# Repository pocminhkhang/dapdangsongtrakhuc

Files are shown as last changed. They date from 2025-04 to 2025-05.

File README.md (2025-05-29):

# ĐẬP DÂNG SÔNG TRÀ KHÚC
Dự án vận hành mô hình đập dâng sông Trà Khúc - Quảng Ngãi

Lĩnh vực dự thi:
-	Phần mềm tin học.
-	Các giải pháp kỹ thuật nhằm ứng phó với biến đổi khí hậu, bảo vệ môi trường và phát triển kinh tế

Giáo viên hướng dẫn:
    Lê Thị Như Huyền 
    SĐT: 0935745789
Tác giả:				Lớp:
    Trần Hoàng Minh Khánh	7B4
    Trần Hoàng Minh Khang	7B4
    Hoàng Minh Tuấn		7B4

IMG_20250529_091230~2

IMAGE ALT TEXT HERE (https://www.youtube.com/watch?v=1BTI75vWhXs)

A.	Ý TƯỞNG:
Nhiều lần cả nhà đi biển, ba em giới thiệu đập dâng và giải thích công dụng của nó. Anh em chúng em rất hứng thú, mong muốn được thấy nước sông dâng lên sẽ rất đẹp. Chờ đợi cũng lâu nhưng chưa thấy đập dâng hoạt động, thành phố Quảng Ngãi vào mùa nắng trơ trọi lòng sông, vậy là 3 anh em chúng em rủ nhau thực hiện dự án vận hành nó (đập dâng sông Trà Khúc)
Ban đầu chúng em chỉ nghĩ đến việc vận hành ngăn nước, xả nước sao cho nước dâng lên – hạ xuống như mong muốn là được. Tuy nhiên trong quá trình tìm hiểu thì mọi chuyện không đơn giản như vậy, trong các video em tìm hiểu được trên mạng về các con đập lớn, người ta đã phải làm cầu cá nhằm đảm bảo tính tự nhiên của hệ sinh thái dòng sông, do vậy đập dâng mô hình phải có cầu cá cho cá bơi ngược dòng về thượng nguồn, đập dâng phải vận hành hoàn toàn tự động theo mực nước thượng nguồn, điều tiết dòng chảy xuống hạ lưu làm sao để không bị nước biển xâm nhập, …
B.	CẤU TẠO MÔ HÌNH SẢN PHẨM
I.	Nguyên vật liệu làm mô hình:

	Tên vật tư	ĐVT	SL	Đơn giá	Thành tiền	Ghi chú
1	Tấm nền (40x80)	Cái	1	100,000 	100,000 	 
2	Sốp dùng làm bờ sông, núi	Tấm	5	20,000 	100,000 	 
3	Làm các phần của đập dâng	Bộ	5	20,000 	100,000 	 
4	Cảm biến mưa	Bộ	1	26,000 	26,000 	 
5	Cảm biến JDS	Bộ	1	81,000 	81,000 	 
6	Cảm biến khoảng cách	Bộ	3	32,000 	96,000 	 
7	Công tắt	Cái	1	2,000 	2,000 	 
8	Servo MG90S	Cái	4	35,000 	140,000 	 
9	Màn hình HMI 2.8inch cảm ứng tích hợp chip ESP32	Cái	1	260,000 	260,000 	 
10	Mạch mở rộng I2C	Cái	1	12,000 	12,000 	 
11	Cầu cá	Cái	1	30,000 	30,000 	 
12	Chip lập trình nhúng ESP32	Cái	1	  88,000 	88,000 	
13	Pin 18650	Cái	1	36,000 	36,000 	 
14	Mạch sạc pin 18650	Cái	1	16,000 	16,000 	 
-	Tổng tiền chi phí nguyên vật liệu: 1.087.000 đ
II.	 Cách lắp ráp, lắp đặt sản phẩm
1.	Mô hình núi, dòng sông, biển:
-	Núi: Làm từ sốp, đắp nhiều lớp lên rồi dùng dao gọt, tạo hình ngọn núi.
-	Bờ sông: Dùng sốp đắp dọc theo 2 bờ tấm nền để tạo bờ sông, hình thành lòng sông và biển ở cuối dòng.
-	Thời gian hoàn thành: 5 ngày
2.	Đảo Ngọc:
-	Dùng sốp làm hòn đảo giữ dòng sông, mô phỏng theo hình Đảo Ngọc thực tế.
-	Thời gian hoàn thành: 1 ngày
3.	Mô hình đập dâng:
-	Đập dâng được làm từ sốp dựng 4 trụ cao, lắp 2 tấm nhựa làm mô hình tấm chắn nước được cắm vào trụ đập.
-	Gắn 3 servo Mg290s vào các trụ như mô hình, 2 servo móc vào 2 tấm nhựa chắn nước, servo còn lại gắn vào mô hình cầu cá
-	Thời gian hoàn thành: 5 ngày
4.	Mô hình cầu cá: 
-	Mô hình cầu cá được làm từ sốp, tạo các bậc thang từ trên xuống dưới, khoét tạo hộc chứa nước, tạo hướng nước chảy 2 bên
-	Thời gian hoàn thành: 3 ngày
5.	Thiết bị đo mực nước:
-	Thiết bị đo mực nước sử dụng cảm biến đo khoảng cách, được cắm vào chip lập trình nhúng ESP32 Dev module và lâp trình để đo khoảng cách từ đầu dò đến mực nước hiện tại và đưa dữ liệu lên đám mây blynk
-	Cảm biến đo khoảng cách dựa vào sóng âm phát ra và thời gian nhận sóng dội âm, từ đó tính toán ra khoảng cách từ đầu dò đến mặt nước. Cảm biến được cắm vào chip lập trình nhúng và được lập trình để đưa số liệu lên đám mây blynk. Trong dự án có 3 đầu dò chiều cao mực nước, các đầu dò được bố trí, đặt tên khác nhau vì thế số liệu từng đầu dò được đưa lên đám mây blynk độc lập nhau.
-	Thời gian hoàn thành: 5 ngày
6.	Thiết bị dò mưa: 
-	Thiết bị báo mưa sử dụng cảm biến mưa cắm vào chip lập trình nhúng ESP32 Dev module và lập trình để đưa số liệu lên đám mây blynk
-	Thiết bị do điện trở của tấm cảm biến, nếu điện trở giảm là do mưa. Chip lập trình đọc giá trị của cảm biến và lưu trên blynk.
-	Thời gian hoàn thành: 2 ngày
7.	Thiết bị đo độ mặn: 
-	Thiết bị đo độ mặn dùng cảm biến TDS cắm vào chip lập trình nhúng ESP32 Dev module và lập trình để đưa số liệu lên đám mây blynk.
-	Thiết bị đo độ mặn của nước đo chỉ số dẫn điện của muối hòa tan trong nước, số liệu đo được sẽ được cập nhật lên đám mây blynk.
-	Thời gian hoàn thành: 2 ngày
8.	Hệ thống điều khiển trung tâm
-	Hệ thống điều khiển trung tâm là màn hình điều khiển HMI LVGL ESP32 WROOM 2.8inch cảm ứng: Màn hình điều khiển tích hợp chip ESP32 lập trình nhúng, một bộ điều khiển gọn nhẹ.
-	Hệ thống điều khiển trung tâm được lập trình để lấy số liệu từ đám mây blynk mà các thiết bị gởi lên để làm số liệu đầu vào nhằm tính toán đưa ra quyết định vận hành đóng – mở cửa xả nước ở cao độ bao nhiêu, đảm bảo mực nước trên và dưới đập dâng đạt yêu cầu, nâng hạ cầu cá để cho cá được đi chuyển thuận lợi nhất.
-	Thời gian hoàn thành: 15 ngày
III.	Nguyên tắc hoạt động, vận hành của mô hình đập dâng
1.	Hệ thống số liệu vận hành của đập dâng:
-	Mực nước mong muốn đạt được theo mùa, hoặc theo biểu đồ độ cao theo thời gian, hoặc theo yêu cầu thực tế vận hành theo số liệu nhập vào.
-	Số liệu nhận được từ các đầu dò được bố trí dọc theo sông: 
+	Đầu dò mưa được bố trí ở thượng nguồn sông, viết tắt: MUA
+	Đầu dò chiều cao mực nước thượng nguồn, viết tắt: MT
+	Đầu dò chiều cao mực nước tại đập dâng, viết tắt: MD
+	Đầu dò chiều cao mực nước tại hạ nguồn, viết tắt: MH
+	Đầu dò độ mặn nước sông hạ nguồn, viết tắt: MAN
-	Thiết lập giá trị mô phỏng vận hành:
+	Có mưa (MUA = 1), không mưa (MUA = 0)
+	Mực nước cao (MTH = 10), bình thường (MTO = 5), thấp tại thượng nguồn (MTL = 0)
+	Mực nước cao (MDH = 10), bình thường (MDO = 5), thấp tại đập dâng (MDL = 0)
+	Mực nước cao (MHH = 10), bình thường (MHO = 5), thấp tại hạ nguồn (MHL = 0)
+	Độ mặn cao (MANH = 10), bình thường (MANO = 5), thấp tại hạ nguồn (MANL = 0)
2.	Điện toán đám mây trung gian:
-	Các đầu dò, cảm biến, đập dâng, tủ điều khiển ở khoảng cách vật lý xa nhau, do vậy để chúng giao tiếp được với nhau thì phải sử dụng wifi, thiết bị sẽ kết nối wifi, đưa số liệu đo đạc được lên đám mây blynk.
-	Bằng cách tạo tài khoản tại blynk, đám mây blynk hỗ trợ tạo các đối tượng dữ liệu nhập vào, lưu tạm, từ đó tủ điều khiển trung tâm có thể truy xuất dữ liệu bất cứ lúc nào để vận hành hệ thống
3.	Nguyên tắc vận hành tự động:
-	Thiết lập cao độ của cầu cá thấp hơn giá trị đầu dò MD 10 cm, tạo dòng chảy êm cho cầu cá, MD thay đổi thì độ cao của cầu cá thay đổi theo.
-	Hệ thống liên tục cập nhật số liệu từ các cảm biến dọc theo sông, lấy mực nước tại đập dâng làm trung tâm cho kịch bản vận hành, từ đó đưa ra quyết định mở đập được tính như sau: 
+	Lưu lượng cần xả hoặc đóng = (MD – MDO) x (hệ số k) x (hệ số quy đổi ra lưu lượng nước cần xả hay đóng dựa trên mong muốn triệt tiêu chênh lệch nhanh hay chậm)
+	Hệ số k là hệ số dùng để tính tỉ lệ điều chỉnh chiều cao mực nước được làm theo thuật toán PID, nhưng do chúng em chưa học đạo hàm và tích phân nên chỉ hiện chỉ dùng tỉ lệ điều chỉnh.
+	Giá trị mặc định cho hệ số k = 2, nghĩa là hệ thống sẽ nâng tốc độ xả hay đóng gấp 2 lần độ chênh lệch mực nước tại đập dâng.
+	Mực nước thượng nguồn MT điều chỉnh hệ số k như sau:
hệ số k = hệ số k + (MT - MTO)/MTO
Khi đó nếu MT > MTO thì hệ số k được cộng thêm, ngược lại sẽ bị trừ đi
+	Trong điều kiện có mưa ở thượng nguồn thì:
hệ số k = hệ số k + 0.01
Khi đó nếu trời có mưa thì việc mở đập sẽ được tác động thêm 0.01. Hệ số 0.01 này chưa được tính chính xác mà chỉ là giả lập, cần tính toán lại theo điều kiện thực tế để có số liệu chính xác hơn.
+	Trong điều kiện hạ nguồn quá cạn nước (MHO - MH) >=4 thì hệ thống sẽ phát thông báo cảnh báo đến người điều hành ra quyết định can thiệp hay không.
+	Trong điều kiện hạ nguồn bị ngập mặn cao (MANH - MAN) <=2 thì hệ số k được tính:
hệ số k = hệ số k + 5%
Việc bù số % bao nhiêu khi ngập mặn cần được tính toán theo số liệu thực tế dòng sông để có được số liệu rửa mặn, số 5% được tạm tính để chạy giả lập mô hình.
+	Sau khi tính toán xong lưu lượng nước cần xả hoặc giữ lại thì ta lấy lưu lượng nước đó chia cho thời gian đáp ứng thay đổi sẽ tính ra diện tích cửa đập cần mở, từ đó tiếp tục chia cho số cửa đập muốn mở và chia cho tổng chiều rộng các đập muốn mở sẽ ra được cao độ cần mở.
+	Sau khi đã có cao độ cần mở thì hệ thống sẽ ra lệch cho servo nâng hoặc hạ đập theo thông số yêu cầu.
-	Trong điều kiện mưa lũ, số liệu MT đạt mức quá cao, gần chạm đỉnh lũ MTH thì hệ thống sẽ gởi cảnh báo lũ cho người điều hành đập dâng ra quyết định can thiệp hay không.
4.	Vận hành thủ công:
Trong điều kiện thời tiết cực đoan, thiên tai, hoặc người điều hành muốn thực hiện các tác vụ để xử lý tức thời vấn đề, người điều hành có thể thực hiện can thiệp trực tiếp bằng cách chuyển qua chế độ vận hành thủ công, qua đó ra lệnh trực tiếp cho hệ thống như sau:
-	Thiết lập cao độ của từng cửa xả từ 0 đến 100
-	Thiết lập cao độ của cầu cá tự động theo chiều cao mực nước hoặc theo cao độ tự chọn từ 0 đến 100
-	Thiết lập cảnh báo hoặc chuyển sang chế độ tự động khi mực nước tại đập dâng hoặc hạ nguồn hoặc thượng nguồn hoặc độ mặn đến điều kiện cần phải chuyển sang chạy tự động hoặc báo động.
IV.	
V.	Ý tưởng mới
-	Các đập dâng hiện nay ở Việt Nam chưa có cầu cá, chưa có hệ thống vận hành theo số liệu đầu dò tại thượng lưu, hạ lưu mà chỉ điều tiết độ cao mực nước hiện tại ở đập dâng.
-	Chúng em chưa tìm thấy có đề tài nào trùng lặp ở Việt Nam nên có thể khẳng định tính mới của dự án.
-	Đặc biệt, đây là dự án vận hành hoàn toàn tự động theo kịch bản chuẩn bị trước hoặc có thể chuyển qua chế độ điều khiển bằng tay.
VI.	Tính sáng tạo
-	Sản phẩm là một dự án IoT có thể hoạt động hoàn toàn tự động, kiểm soát được số liệu từ xa cũng như được báo cáo cập nhật liên tục, nó đáp ứng được sự biến động bất ngờ của thời tiết, chủ động đưa ra cảnh báo để vận hành sớm hơn khi thiên tai ập đến.
VII.	Khả năng áp dụng thực tiển
-	Sản phẩm của chúng em được dựng lên từ thực tế đập dâng sông Trà Khúc – Quảng Ngãi, mong muốn áp dụng vào dự án Đập dâng sông Trà Khúc.
-	Sản phẩm được mô phỏng để có thể tự động xả nước khi mực nước thượng nguồn vượt ngưỡng yêu cầu, tự động tích nước khi mực nước xuống qua số liệu liên tục được cập nhật tự động qua hệ thống.
-	Hạn chế môi trường hạ lưu không bị ngập mặn, không thay đổi môi trường sinh sống tự nhiên của các sinh vật sống trên sông.

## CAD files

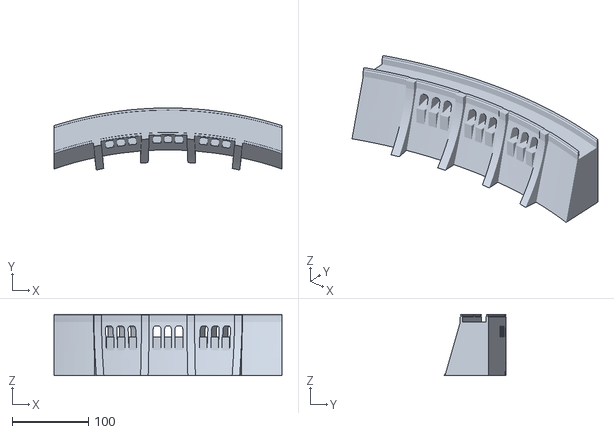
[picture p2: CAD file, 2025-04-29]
Model/DAM.stl
298.7 x 81.4 x 80.0

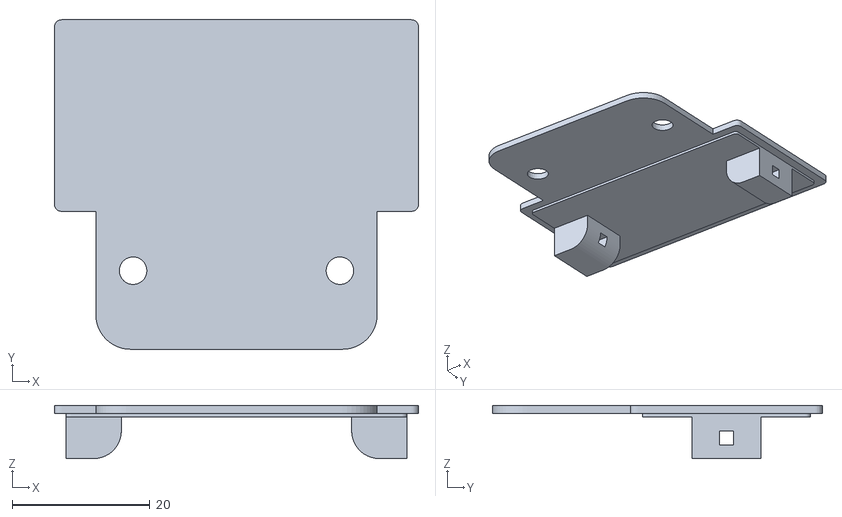
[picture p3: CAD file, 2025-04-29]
Model/HC-SR04 case/ultrasonic_-_pokrywa.stl
52.8 x 47.8 x 7.70

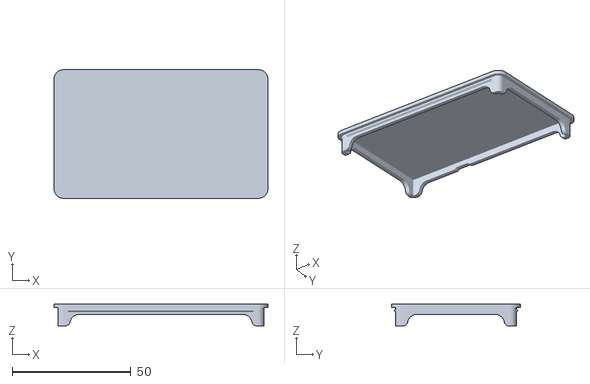
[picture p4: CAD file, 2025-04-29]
Model/HMI LVGL ESP32 2.8inch case/28inch-back-cover.stl
90.0 x 54.1 x 9.20

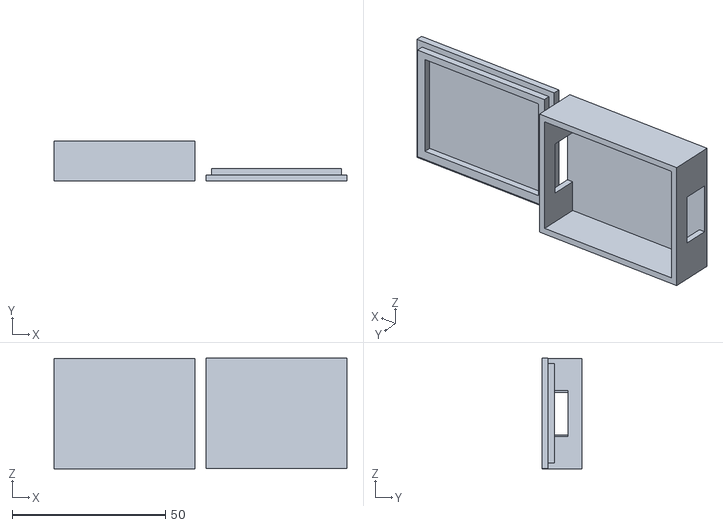
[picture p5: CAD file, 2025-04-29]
Model/TDS metter case/keyestudio_TDS_Meter_V1.0_v4.stl
95.7 x 13.0 x 36.1

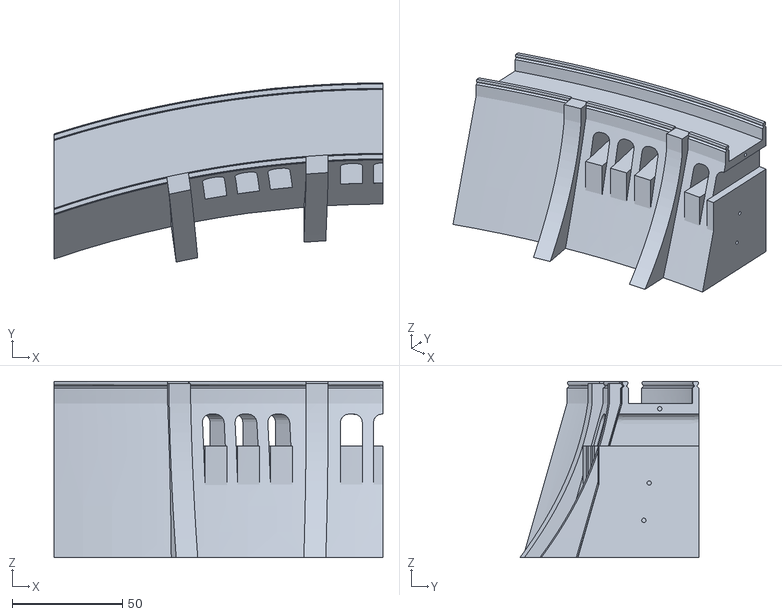
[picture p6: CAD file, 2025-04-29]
Model/dam_left.stl
149.4 x 81.4 x 80.0

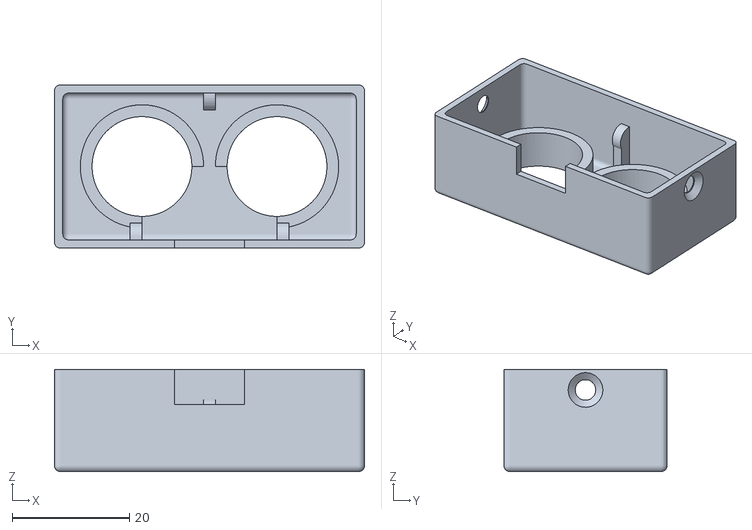
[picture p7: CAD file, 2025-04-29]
Model/HC-SR04 case/ustrasonic_-_korpus.stl
52.8 x 27.8 x 17.4

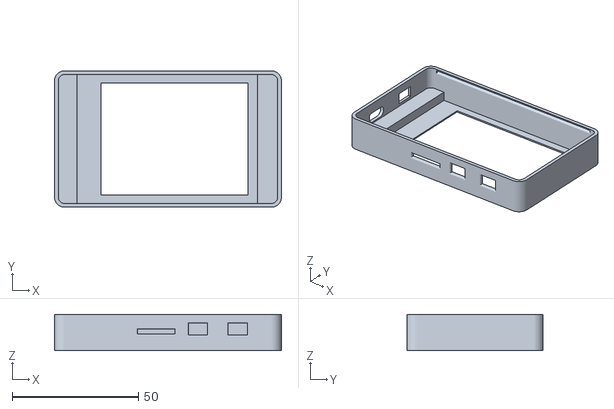
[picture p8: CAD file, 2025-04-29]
Model/HMI LVGL ESP32 2.8inch case/28inch-front-case.stl
90.0 x 54.1 x 14.3

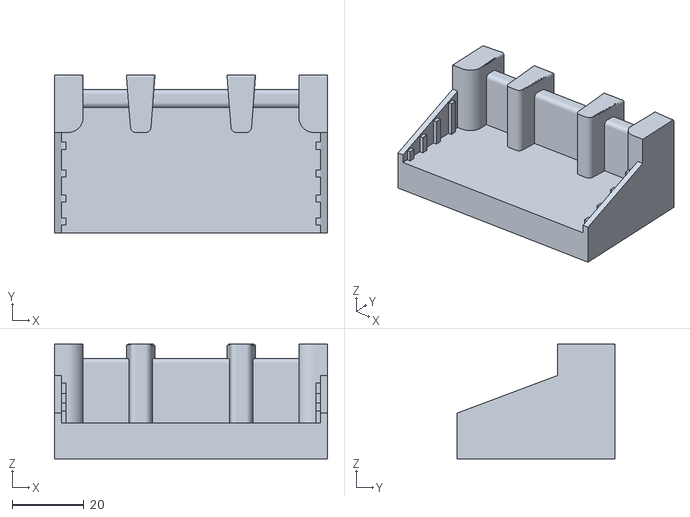
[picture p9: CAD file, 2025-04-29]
Model/Weir.stl
76.0 x 44.0 x 32.0

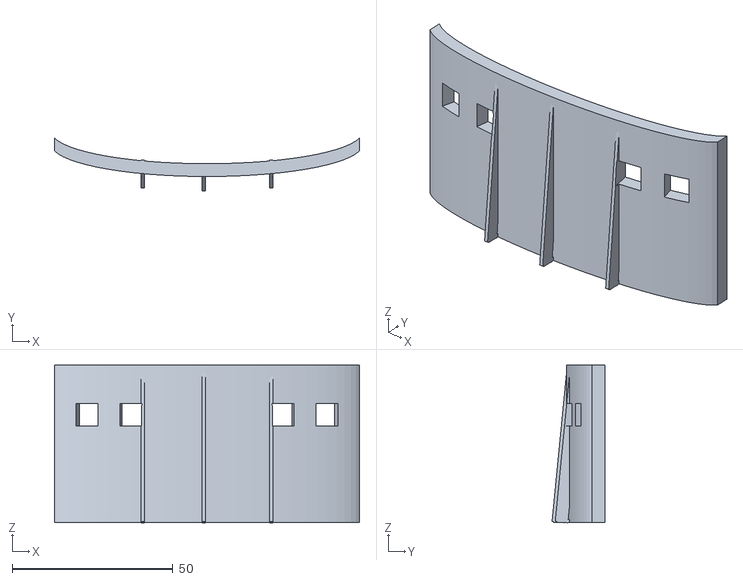
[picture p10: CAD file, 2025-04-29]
Model/dam2.stl
95.0 x 16.5 x 49.1

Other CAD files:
Model/dam_right.stl

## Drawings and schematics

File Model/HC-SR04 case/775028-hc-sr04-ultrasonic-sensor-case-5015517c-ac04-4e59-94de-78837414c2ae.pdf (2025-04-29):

## HC-SR04 Ultrasonic

## sensor case

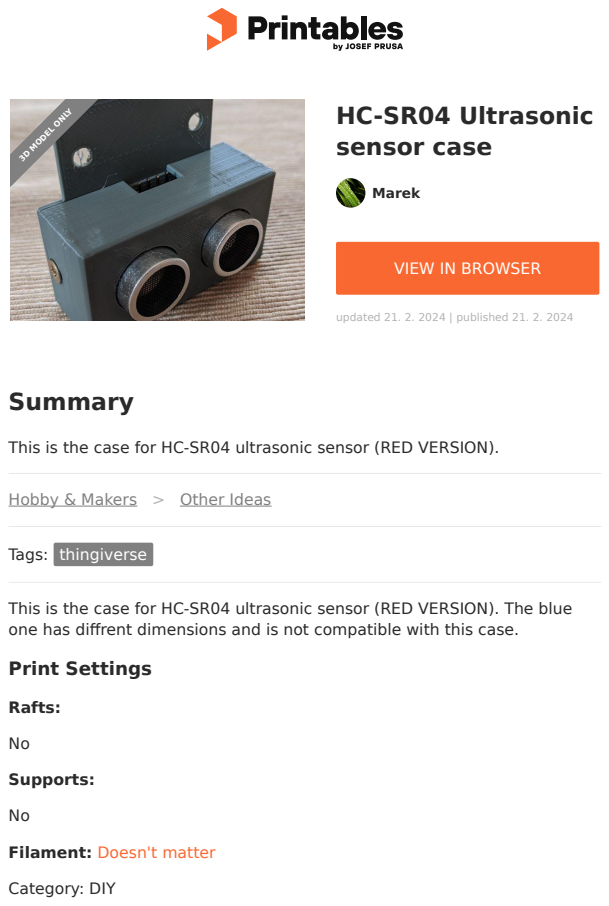
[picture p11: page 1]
Summary; Tags: thingiverse; Print Settings; Rafts:; Supports:; Category: DIY; Marek; updated 21. 2. 2024 | published 21. 2. 2024; 3D MODEL ONLY

VIEW IN BROWSER (https://printables.com/model/775028-hc-sr04-ultrasonic-sensor-case)

This is the case for HC-SR04 ultrasonic sensor (RED VERSION).

Hobby & Makers (https://printables.com/model?categoryId=48) > Other Ideas (https://printables.com/model?categoryId=82)

This is the case for HC-SR04 ultrasonic sensor (RED VERSION). The blue
one has diffrent dimensions and is not compatible with this case.

Filament: Doesn't matter (http://www.amazon.com/s?url=search-alias&field-keywords=Doesn%27t+matter+PLA)

# Model files

Find source .stl files on Thingiverse.com (https://www.thingiverse.com/thing:4329198)

## License

This work is licensed under a
Creative Commons (4.0 International License)

Attribution—Noncommercial—Share Alike (http://creativecommons.org/licenses/by-nc-sa/4.0/)

### ✖ | Sharing without ATTRIBUTION

✔ | Remix Culture allowed
✖ | Commercial Use
✖ | Free Cultural Works
✖ | Meets Open Definition

ustrasonic_-_korpus.stl

ultrasonic_-_pokrywa.stl

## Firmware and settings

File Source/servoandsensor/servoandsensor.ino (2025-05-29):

#define BLYNK_TEMPLATE_ID "TMPL6HOJBzMD0"
#define BLYNK_TEMPLATE_NAME "ESP32 SensorUpdater"
#define BLYNK_AUTH_TOKEN "hJgqjTXA5cPqRychjZos7jHKfc2ZAhlD"


#define BLYNK_PRINT Serial

#include <WiFi.h>
#include <WiFiClient.h>
#include <BlynkSimpleEsp32.h>
#include <ESP32Servo.h>
#include <ESPWifiConfig.h>


BlynkTimer timer;

int ServerPort = 80;
int Config_reset_btn = -1;

boolean debug = true; 

ESPWifiConfig WifiConfig("DapDang2", ServerPort, Config_reset_btn, false, "","", debug);

#define NO_CONNECTION_RESTART_DELAY 3600000 //ms, 1 hour
#define NO_CONNECTION_GO_WILD_DELAY 1800000 //ms, 30 minutes


unsigned long last_wifi_connect_time = 0;
unsigned long reconnect_delay = 10000;

boolean ensure_wifi_connectivity(unsigned long no_conn_go_wild_delay, unsigned long no_conn_restart_delay);

bool connectyet = false;//To check the connect


const int servoPinfish = 12;
const int servoPin1    = 14;
const int servoPin2    = 27;
const int servoPin3    = 26;

Servo servofishladder;
Servo servo1;
Servo servo2;
Servo servo3;

bool autoFishMode = false;
int autoMode= 0;

int fishServoValue = 0;
int servo1Value    = 0;
int servo2Value    = 0;
int servo3Value    = 0;

int Thuong_Mua = 0;
int Thuong_WL = 0;
int Dap_WL = 0;
int Ha_WL = 0;
int Ha_SL = 0;
int Thuong_H = 15;
int Thuong_L = 5;
int Dap_H = 12;
int Dap_L = 5;
int Ha_H = 8;
int Ha_L = 3;
int DamWaterLevel = 8;
int VanHigh = 0;

int getangle(int high) {
  return map(high, 0, 20, 0, 180);
}

void myTimerEvent()
{
  Blynk.syncVirtual(V0);
  Blynk.syncVirtual(V1);
  Blynk.syncVirtual(V2);
  Blynk.syncVirtual(V3);
  Blynk.syncVirtual(V4);
  Blynk.syncVirtual(V6);
  Blynk.syncVirtual(V7);
}

BLYNK_WRITE(V6) {
  autoFishMode = (param.asInt() == 1);  // 1 thì bật chế độ tự động thang cá
  if (autoFishMode == true) {
    servofishladder.write(getangle(Dap_WL));
  } else {
    servofishladder.write(fishServoValue);
  }
}

BLYNK_WRITE(V0) {  
  Thuong_Mua = param.asInt();
  Serial.println(Thuong_Mua);   
}
BLYNK_WRITE(V1) {
  Thuong_WL = param.asInt();
  Serial.print("Thuong WL__: ");
  Serial.println(Thuong_WL);
}
BLYNK_WRITE(V2) {  Dap_WL  = param.asInt(); }
BLYNK_WRITE(V3) {  Ha_WL   = param.asInt(); }
BLYNK_WRITE(V4) {  Ha_SL  = param.asInt(); }
BLYNK_WRITE(V14) {
  int x = param.asInt();
  fishServoValue = map(x, 0, 100, 0, 180);
}
BLYNK_WRITE(V15) {
  int y = param.asInt();
  servo1Value = map(y, 0, 100, 0, 180);
}
BLYNK_WRITE(V16) {
  int z = param.asInt();
  servo2Value = map(z, 0, 100, 0, 180);
}
BLYNK_WRITE(V17) {
  int t = param.asInt();
  servo3Value = map(t, 0, 100, 0, 180);
}

void AutoVan(){                      
  if ((Thuong_WL >= Thuong_H)||(Dap_WL >= Dap_H)) {
    Serial.println("Nếu mực nước thượng nguồn cao");
    servo1Value = 180;
    servo2Value = 180;
    servo3Value = 180;
  } 
  if ((Thuong_WL > 5 && Thuong_WL < 15) || ((Dap_WL > Dap_L) && (Dap_WL < Dap_H))) {
    int d = Dap_WL - DamWaterLevel;
    if (d > 0) {
      VanHigh = 10*d;
    }
    else if (d < 0){
      VanHigh = 10/(abs(d));
    }
    else{
      VanHigh = 0;
    }
    servo1Value = VanHigh;
    servo2Value = VanHigh;
    servo3Value = VanHigh;
    Serial.println("Nếu mực nước thượng nguồn lớn hơn 5 và nhỏ hơn 15");
  }

  if (Ha_SL >=600 && Ha_SL <=799){
    servo1Value = VanHigh + 30;
    servo2Value = VanHigh + 40;
    servo3Value = VanHigh + 30;
  }
  if (Ha_SL >=800){
    servo1Value = VanHigh + 50;
    servo2Value = VanHigh + 60;
    servo3Value = VanHigh + 50;
    Serial.println("Độ mặn");
  }
}

BLYNK_WRITE(V7) {
  autoMode = param.asInt();  // 1 thì bật chế độ tự động van
  if (autoMode == 1) { 
    AutoVan();
    servo1.write(servo1Value);
    servo2.write(servo2Value);
    servo3.write(servo3Value);
    Serial.println("Autovan...");
  }
  else {
    servo1.write(servo1Value);
    servo2.write(servo2Value);
    servo3.write(servo3Value);
    Serial.print("servo1Value: "); Serial.println(servo1Value);
    Serial.print("servo2Value: "); Serial.println(servo2Value);
    Serial.print("servo3Value: "); Serial.println(servo3Value);
  }
}


void setup() {
  Serial.begin(115200);
  
  if (WifiConfig.initialize() == AP_MODE)//To check the mode,here AP mode
  {
  WifiConfig.Start_HTTP_Server(600000); 

  Serial.println("ESP is running in AP MODE");
  Serial.print("Connect to it's Wifi named: ");
  Serial.println(WifiConfig.get_AP_name());
  }
  else //Client mode
  {
    //dont do anything
  }
  WifiConfig.print_settings();
  WifiConfig.ESP_debug("Hello");

  while(connectyet == false){       //check the connect
    WifiConfig.handle(reconnect_delay);
    if (ensure_wifi_connectivity(NO_CONNECTION_GO_WILD_DELAY, NO_CONNECTION_RESTART_DELAY)) 
    {//if connect success
      connectyet = true;
    }
    else
    {//if Connect fail
      connectyet = false;
      WifiConfig.ESP_reset_settings();
    }
  }

  Blynk.begin(BLYNK_AUTH_TOKEN, WifiConfig.setting[WIFI_SSID].value, WifiConfig.setting[WIFI_PASS].value);
  timer.setInterval(1000L, myTimerEvent);
  Serial.println("blynk");
  servofishladder.attach(servoPinfish);
  servo1.attach(servoPin1);
  servo2.attach(servoPin2);
  servo3.attach(servoPin3);
  servo1.write(90);
  servo2.write(90);
  servo3.write(90);
  servofishladder.write(90);
  delay(2000);
  servo1.write(0);
  servo2.write(0);
  servo3.write(0);
  servofishladder.write(0);
  timer.setInterval(1000L, myTimerEvent);
}

void loop() {
  Blynk.run();
  timer.run();
}

boolean ensure_wifi_connectivity(unsigned long no_conn_go_wild_delay, unsigned long no_conn_restart_delay){
  //Access point mode
  if (WifiConfig.ESP_mode == AP_MODE)
  {
    if (millis() > no_conn_go_wild_delay)
    {
      WifiConfig.goWild();
    }
  }
  else
  {
    if (WifiConfig.ESP_mode == CLIENT_MODE)
    {
      if (WifiConfig.wifi_connected)
      {
        last_wifi_connect_time = millis();
        reconnect_delay = 10000;
        return true;
      }
      else
      {
        reconnect_delay = 30000; 

        if ((millis() - last_wifi_connect_time) > no_conn_restart_delay)
        {
          Serial.println("Restarting...");
          ESP.restart();          
        }
        else if ((millis() - last_wifi_connect_time) > no_conn_go_wild_delay)
        {
          if (WifiConfig.goWild() > 0)
          {
            Serial.println("Connecting to open WiFi");
          }
          else
          {
            WifiConfig.wifiscan();
            delay(20000); 
          }
        }
      }
    }
  }
  return false;
}

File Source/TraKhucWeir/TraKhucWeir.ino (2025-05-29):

#define BLYNK_TEMPLATE_ID "TMPL6HOJBzMD0"
#define BLYNK_TEMPLATE_NAME "ESP32 SensorUpdater"
#define BLYNK_AUTH_TOKEN "hJgqjTXA5cPqRychjZos7jHKfc2ZAhlD"

#define BLYNK_PRINT Serial

#include <WiFi.h>
#include <WiFiClient.h>
#include <BlynkSimpleEsp32.h>
#include <ESPWifiConfig.h>

int Apin = 34;
int TDSpin = 36;
int TrigD = 14;
int EchoD = 13;
int TrigT = 33;
int EchoT = 25;
int TrigH = 32;
int EchoH = 35;

BlynkTimer timer;

int ServerPort = 80;
int Config_reset_btn = -1;

boolean debug = false; 

ESPWifiConfig WifiConfig("DapDang", ServerPort, Config_reset_btn, false, "", "", debug);

#define NO_CONNECTION_RESTART_DELAY 3600000 //ms, 1 hour
#define NO_CONNECTION_GO_WILD_DELAY 1800000 //ms, 30 minutes


unsigned long last_wifi_connect_time = 0;
unsigned long reconnect_delay = 10000;

boolean ensure_wifi_connectivity(unsigned long no_conn_go_wild_delay, unsigned long no_conn_restart_delay);

uint16_t WaterLevelSensor(int Trigpin ,int Echopin){
  digitalWrite(Trigpin, LOW);
  delayMicroseconds(2);
  digitalWrite(Trigpin,  HIGH);
  delayMicroseconds(10);
  digitalWrite(Trigpin, LOW);

  const unsigned long duration = pulseIn(Echopin, HIGH, 30000);

  if (duration == 0) return 999;

  int distance= duration/29/2;
  if (distance>20){distance = 20;}
  int value = 20 - distance;
  return value;
}

bool connectyet = false;

void myTimerEvent()
{
  int RawSensorValues = analogRead(Apin);

  float rawValue = analogRead(TDSpin);
  float volt = (rawValue / 4095.0)*2.3;
  int TDSValue = (133.42 * volt * volt * volt - 255.86 * volt * volt + 857.39 * volt) * 0.5;
  int Salinity = TDSValue * 0.64;
  int SalinityValue = map(Salinity, 0, 717, 0, 1000);
  int sensorValue = map(RawSensorValues, 0, 4095 ,0 ,1000);
  if (sensorValue <= 800){
    Blynk.virtualWrite(V0, 1);
  }
  else{
    Blynk.virtualWrite(V0, 0);
  }
  Blynk.virtualWrite(V4, SalinityValue);
  Blynk.virtualWrite(V2, WaterLevelSensor(TrigD ,EchoD));
  Blynk.virtualWrite(V3, WaterLevelSensor(TrigH ,EchoH));
  Blynk.virtualWrite(V1, WaterLevelSensor(TrigT ,EchoT));
}

void setup() {
  Serial.begin(115200);
  Serial.println("Start");
  Serial.println(WiFi.macAddress());

  if (WifiConfig.initialize() == AP_MODE)
  {
    WifiConfig.Start_HTTP_Server(600000); 

    Serial.println("ESP is running in AP MODE");
    Serial.print("Connect to it's Wifi named: ");
    Serial.println(WifiConfig.get_AP_name());
  }
  else 
  {
    //
  }
  WifiConfig.print_settings();
  WifiConfig.ESP_debug("Hello");

  while(connectyet == false){
    WifiConfig.handle(reconnect_delay);
    if (ensure_wifi_connectivity(NO_CONNECTION_GO_WILD_DELAY, NO_CONNECTION_RESTART_DELAY)) 
    {
      connectyet = true;
      Serial.println("Connected");
    }
    else
    {
      connectyet = false;
      WifiConfig.ESP_reset_settings();
    }
  }

  Serial.println(WifiConfig.setting[WIFI_SSID].value);
  Serial.println(WifiConfig.setting[WIFI_PASS].value);
  Blynk.begin(BLYNK_AUTH_TOKEN, WifiConfig.setting[WIFI_SSID].value, WifiConfig.setting[WIFI_PASS].value);
  Serial.println("Blynk");

  timer.setInterval(2000L, myTimerEvent);
  pinMode(TrigD, OUTPUT);
  pinMode(EchoD, INPUT);
  pinMode(TrigT, OUTPUT);
  pinMode(EchoT, INPUT);
  pinMode(TrigH, OUTPUT);
  pinMode(EchoH, INPUT);
  pinMode(Apin, INPUT);
  pinMode(TDSpin, INPUT);
}

void loop()  {
  Blynk.run();
  timer.run();
}

boolean ensure_wifi_connectivity(unsigned long no_conn_go_wild_delay, unsigned long no_conn_restart_delay)
{
  //Access point mode
  if (WifiConfig.ESP_mode == AP_MODE)
  {
    if (millis() > no_conn_go_wild_delay)
    {
      WifiConfig.goWild();
    }
  }
  else
  {
    if (WifiConfig.ESP_mode == CLIENT_MODE)
    {
      if (WifiConfig.wifi_connected)
      {
        last_wifi_connect_time = millis();
        reconnect_delay = 10000;
        return true;
      }
      else
      {
        reconnect_delay = 30000; 

        if ((millis() - last_wifi_connect_time) > no_conn_restart_delay)
        {
          Serial.println("Restarting...");
          ESP.restart();          
        }
        else if ((millis() - last_wifi_connect_time) > no_conn_go_wild_delay)
        {
          if (WifiConfig.goWild() > 0)
          {
            Serial.println("Connecting to open WiFi");
          }
          else
          {
            WifiConfig.wifiscan();
            delay(20000); 
          }
        }
      }
    }
  }
  return false;
}

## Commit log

2025-04-29 Cập nhật model
    [28inch-back-cover.stl, 28inch-front-case.stl, DAM.stl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]
2025-05-29 Upload source ServoAndSensor
